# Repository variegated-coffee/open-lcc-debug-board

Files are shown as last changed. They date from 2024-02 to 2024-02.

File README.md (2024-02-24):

# Open LCC Debug Board

Schematics and PCB files for the Open LCC debug board. Licensed under the CERN OHL-P license.

The Debug Board exposes SWD, JTAG, USB and Reset/GPIO0/Bootsel for the RP2040 and ESP32-S3 on the Open LCC Main Board.

It also has an optional boost converter to provide 12V instead of 5V as VIN to the Open LCC Main board. When using the color TFT, this doesn't matter at all. When using the OLED, the OLED is dimmer when powered using 5V. You probably don't need this boost converter.

## Disclaimer

Anything you do with this, you do at your own risk. Components have been fried already during the course of this project. Your machine uses both line voltage power, high pressured hot water, steam and other dangerous components. Risks include but are not limited to, damaging the machine, personal injury, property damage and summoning dead Cthulhu from his sleep at R'lyeh.

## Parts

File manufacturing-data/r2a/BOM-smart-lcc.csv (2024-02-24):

Comment | Designator | Footprint | LCSC
F0503-ZV-24-20T-R | J7 | FPC_24 | C481246
USB_B_Micro | J1,J11 | USB_Micro-B_Molex-105133-0001 | C586226

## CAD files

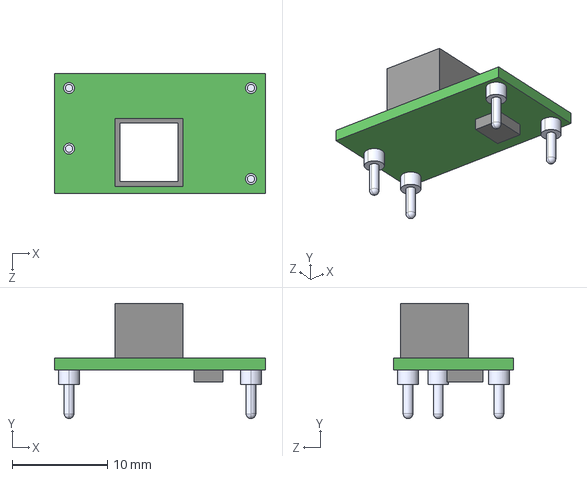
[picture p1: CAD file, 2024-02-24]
PTN04050CAD/PTN04050CAD.step
22.1 x 12.1 x 12.6 mm

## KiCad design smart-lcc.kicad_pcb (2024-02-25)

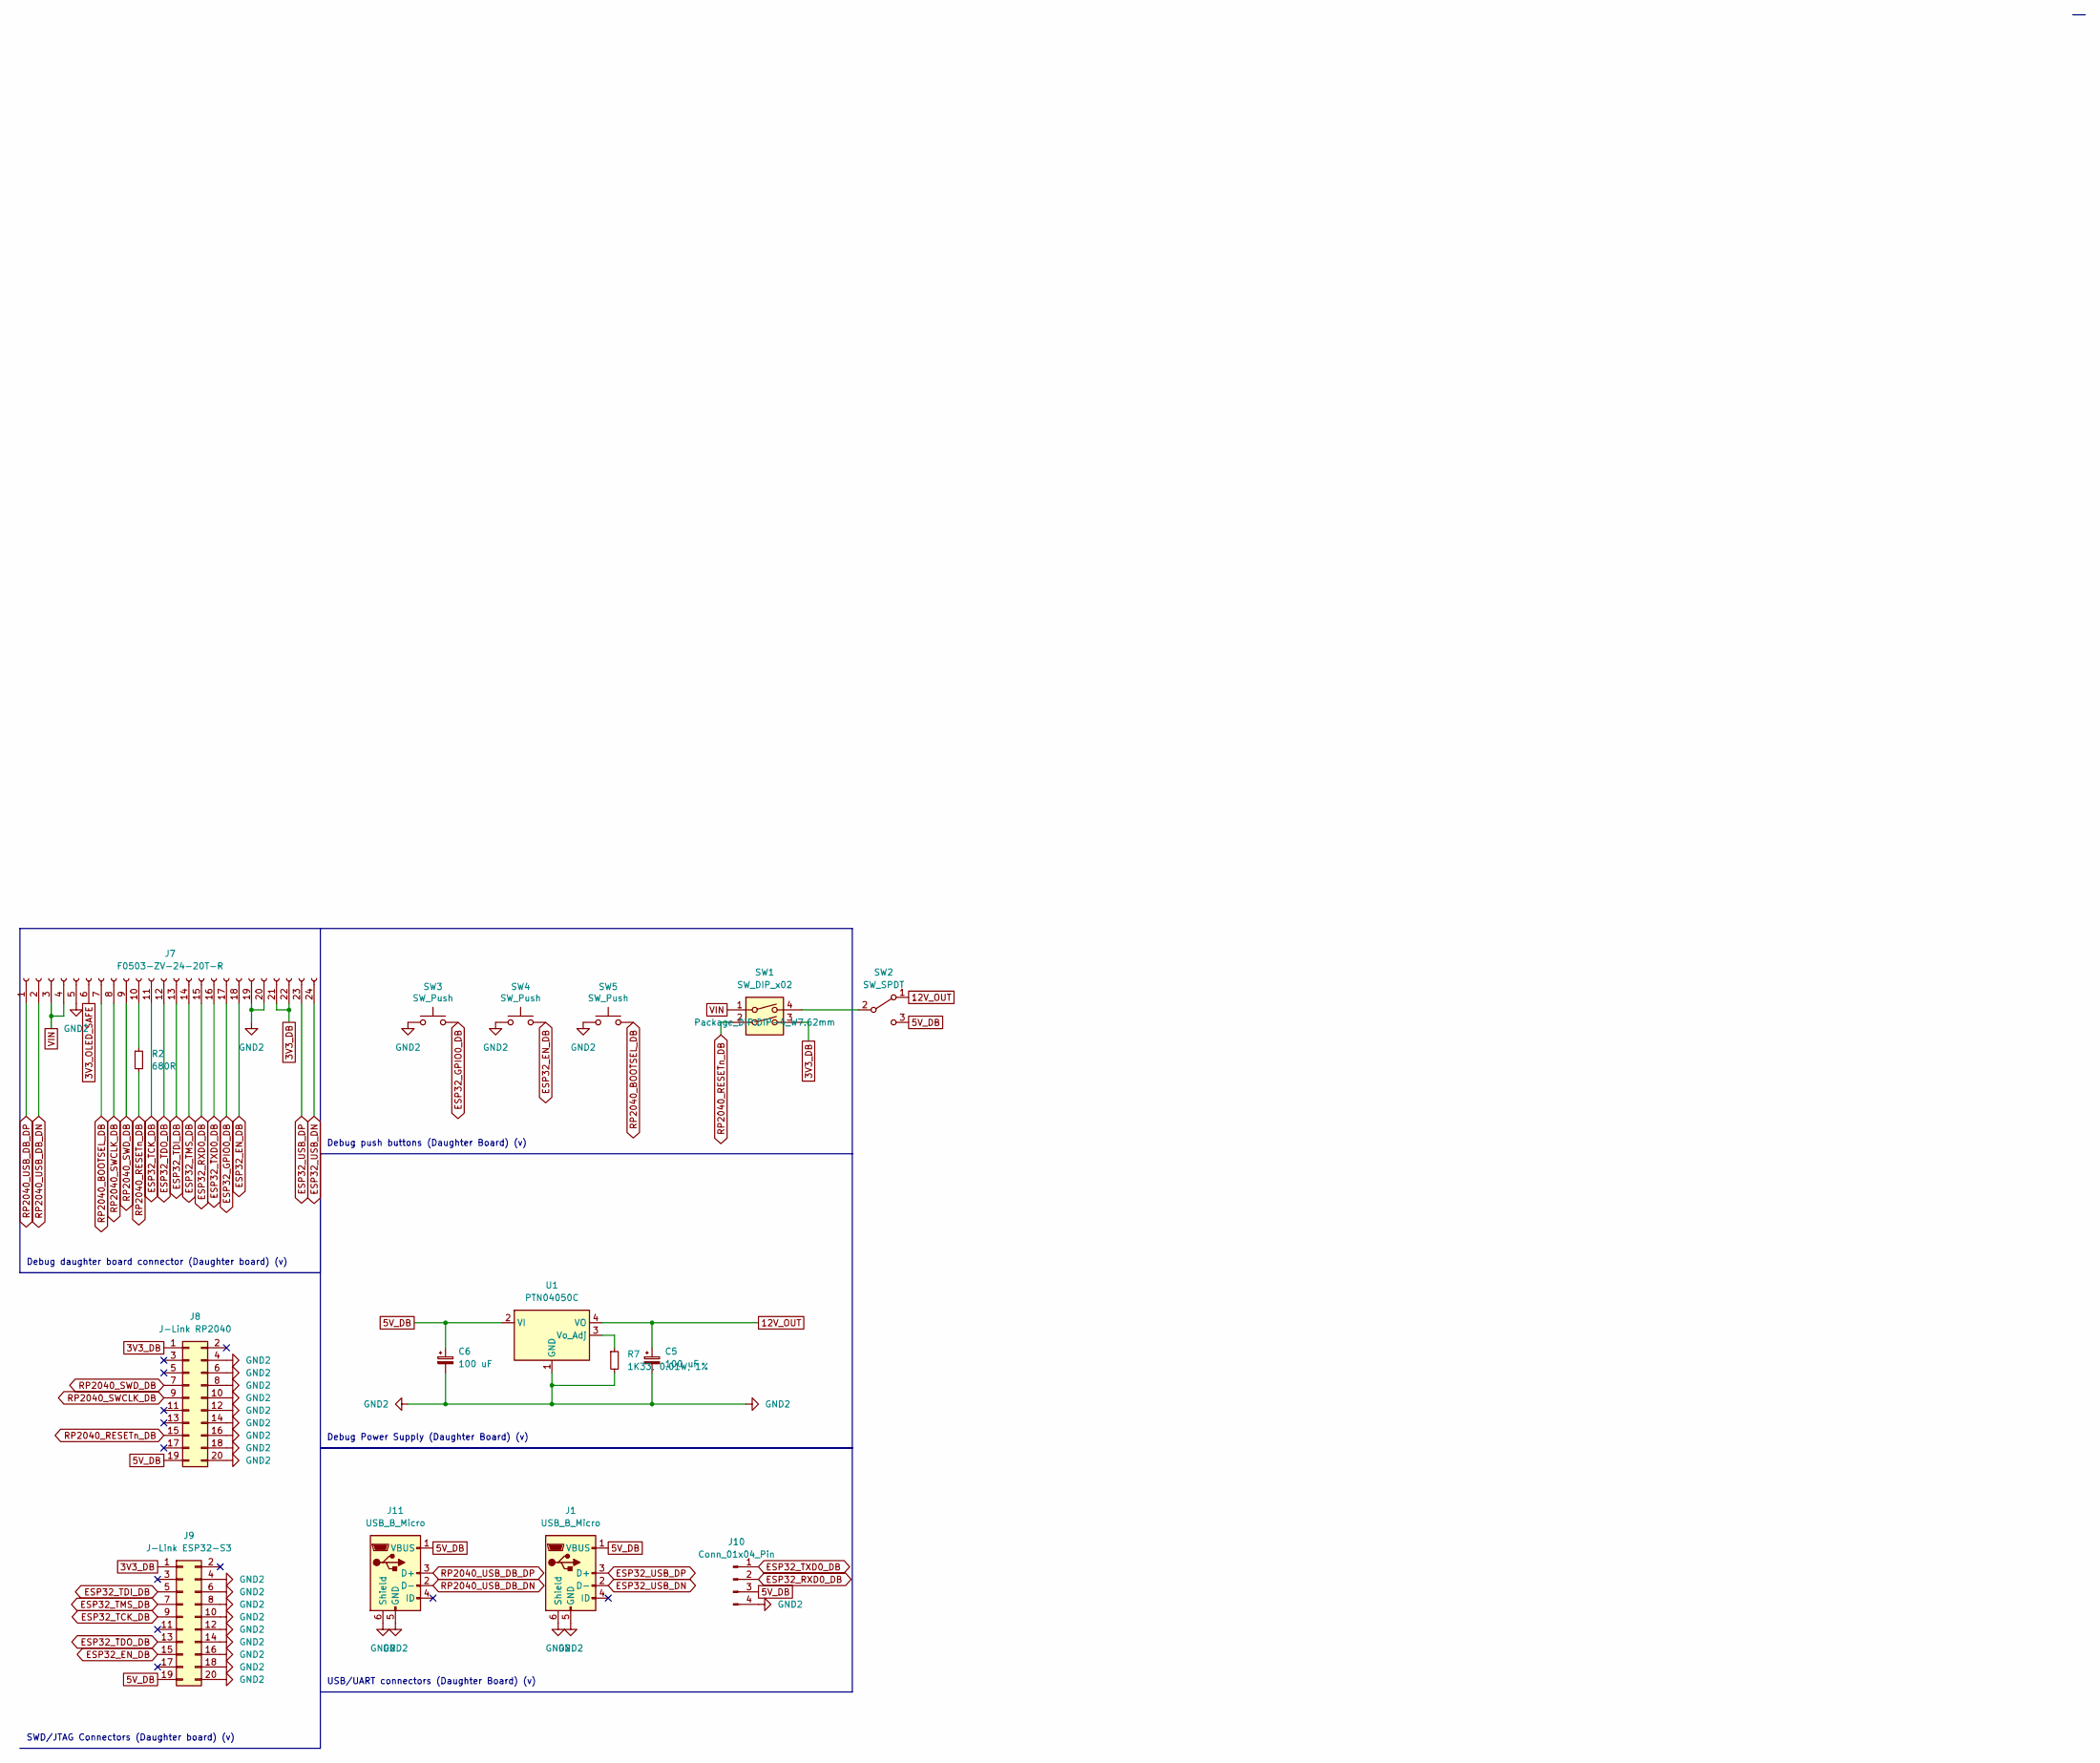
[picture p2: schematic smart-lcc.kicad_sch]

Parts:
C5, C6: 100 uF; CP_Radial_D7.5mm_P2.50mm
J1, J11: USB_B_Micro; USB_Micro-B_Molex-105133-0001; LCSC C586226
J7: F0503-ZV-24-20T-R; FPC_24; JLCPCB Basic N
J8: J-Link RP2040; IDC-Header_2x10_P2.54mm_Vertical
J9: J-Link ESP32-S3; IDC-Header_2x10_P2.54mm_Vertical
J10: Conn_01x04_Pin; PinHeader_1x04_P2.54mm_Vertical
R2: 680R; R_Axial_DIN0204_L3.6mm_D1.6mm_P7.62mm_Horizontal
R7: 1K33, 0.01W, 1%; R_Axial_DIN0204_L3.6mm_D1.6mm_P7.62mm_Horizontal
SW1: SW_DIP_x02; DIP-4_W7.62mm
SW2: SW_SPDT; PinHeader_1x03_P2.54mm_Vertical
SW3, SW4, SW5: SW_Push; ADTSMW65
U1: PTN04050C; CONV_PTN04050CAD

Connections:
3V3_DB: J7.21, J7.22, J8.1, J9.1, SW1.3
3V3_OLED_SAFE: J7.6
5V_DB: C6.1, J1.1 (VBUS), J8.19, J9.19, J10.3, J11.1 (VBUS), SW2.3 (C), U1.2 (VI)
12V_OUT: C5.1, SW2.1 (A), U1.4 (VO)
ESP32_EN_DB: J7.18, J9.15, SW4.2
ESP32_GPIO0_DB: J7.17, SW3.2
ESP32_RXD0_DB: J7.15, J10.2
ESP32_TCK_DB: J7.11, J9.9
ESP32_TDI_DB: J7.13, J9.5
ESP32_TDO_DB: J7.12, J9.13
ESP32_TMS_DB: J7.14, J9.7
ESP32_TXD0_DB: J7.16, J10.1
ESP32_USB_DN: J1.2 (D-), J7.24
ESP32_USB_DP: J1.3 (D+), J7.23
GND2: C5.2, C6.2, J1.5 (GND), J1.6 (Shield), J7.5, J7.19, J7.20, J8.4, J8.6, J8.8, J8.10, J8.12, J8.14, J8.16, J8.18, J8.20, J9.4, J9.6, J9.8, J9.10, J9.12, J9.14, J9.16, J9.18, J9.20, J10.4, J11.5 (GND), J11.6 (Shield), R7.2, SW3.1, SW4.1, SW5.1, U1.1 (GND)
unnamed: J7.10, R2.1
unnamed: SW1.4, SW2.2 (B)
unnamed: R7.1, U1.3 (Vo_Adj)
RP2040_BOOTSEL_DB: J7.7, SW5.2
RP2040_RESETn_DB: J8.15, R2.2, SW1.2
RP2040_SWCLK_DB: J7.8, J8.9
RP2040_SWD_DB: J7.9, J8.7
RP2040_USB_DB_DN: J7.2, J11.2 (D-)
RP2040_USB_DB_DP: J7.1, J11.3 (D+)
VIN: J7.3, J7.4, SW1.1

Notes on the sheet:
Debug daughter board connector (Daughter board) (v)
SWD/JTAG Connectors (Daughter board) (v)
USB/UART connectors (Daughter Board) (v)
Debug push buttons (Daughter Board) (v)
Debug Power Supply (Daughter Board) (v)

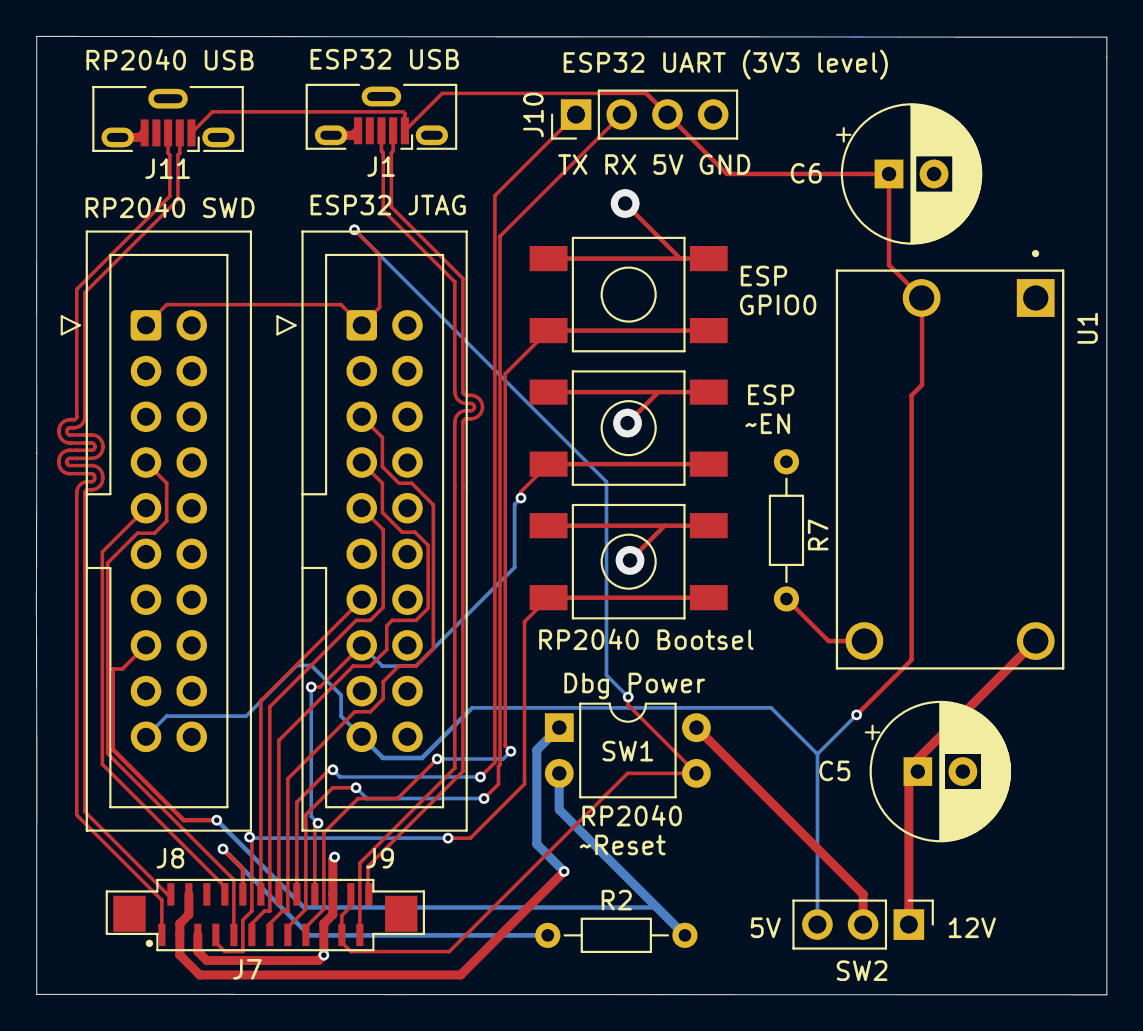
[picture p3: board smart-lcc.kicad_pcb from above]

Board: 2 copper layers, 59.5 x 53.2 mm, 16 parts (0 on the bottom side), 24 nets.

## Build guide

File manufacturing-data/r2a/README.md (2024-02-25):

# How to order and assemble

## PCB and PCBA manufacturer

This directory contains Gerber files for the PCB, a BOM file with LCSC numbers for ordering with JLCPCB, and a CPL file.

### Orientations

Be careful with the orientation of the FPC connector on both this and the main board. Pin 1 is indicated on the board. When placed correctly on both the Open LCC and Debug board, you should use an FPC cable with *connectors on opposite sides*. If for some reason the connector is incorrectly oriented, you'll still be able to use the boards, but you may need an FPC cable with connectors on the *same* side. 

Orientations in general are a bit of a pain. I recommend checking the "Confirm production files" option on JLCPCB, to be able to verify that the orientations of all the components match the PCB and schematic.

## Parts you'll need from other vendors

The BOM in the file isn't complete; you'll need a few other parts, all of which are hand soldered. Below is a table, including links to Digikey when the item is available there.

| Designator  | Part name | Notes | URL (for one vendor, usually there are others) |
|---|---|---|---|
| J8, J9 | 2x10 pin IDC Male header | Optional, intended to be used with J-Link | https://www.digikey.se/en/products/detail/sullins-connector-solutions/SBH11-PBPC-D10-ST-BK/1990065 |
| SW3-SW5 | Omron B3S-1000 | | https://www.digikey.se/en/products/detail/omron-electronics-inc-emc-div/B3S-1000/20686 |
| SW1 | 2x DIP switch | | https://www.digikey.se/en/products/detail/grayhill-inc/78B02T/726239 |
| SW2 | 2.54 mm SPDT switch | Can be replaced with a 2 or 3 pin header and a jumper | https://www.digikey.se/en/products/detail/eao/09-03290-01/8733106 |
| R2 | 680R Resistor | Current limiting resistor for RP2040 RESETn | https://www.digikey.se/en/products/detail/yageo/MFR-25FBF52-680R/9138201 |
| U2 | PTN04050C Boost module | Optional, supplies 12V to main board VIN instead of 5V. | https://www.digikey.se/en/products/detail/texas-instruments/PTN04050CAD/864519 |
| R7 | 1K33 Resistor | Only required when using PTN0405C | https://www.digikey.se/en/products/detail/yageo/MFR-25FBF52-1K33/13036 |
| C5, C6 | 100 µF, 16 V electrolytic cap | Only required when using PTN04050C | https://www.digikey.se/en/products/detail/panasonic-electronic-components/EEA-GA1C101/2504576 |

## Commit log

2024-02-24 Initial import
    [PTN04050CAD.step, smart-lcc.kicad_pcb, smart-lcc.kicad_sch]
2024-02-24 Added manufacturing data
    [BOM-smart-lcc.csv, smart-lcc.kicad_sch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]
2024-02-24 Manufacturing instructions
    [smart-lcc.kicad_pcb]
2024-02-25 Updated with value for R2 resistor
    [smart-lcc.kicad_pcb, smart-lcc.kicad_sch]

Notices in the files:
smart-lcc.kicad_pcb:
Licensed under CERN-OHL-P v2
